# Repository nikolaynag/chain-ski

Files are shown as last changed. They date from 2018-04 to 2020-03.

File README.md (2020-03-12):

# Chain ski

This is an experimental project dedicated to a new concept of running gear. The
idea is to make something similar to continuous track, but with rollers fixed
on chain links instead of a vehicle. Each link of the track chain is a bogie
that rolls over a closed-loop rail mounted on the vehicle. Two adjacent links
share same axle. Rail contour is carefully calculated to provide continuous
whole-loop rolling. The mechanism does not involve any sliding friction and
in theory can provide a good alternative to inline  skates, at least on rough
or soft surfaces.

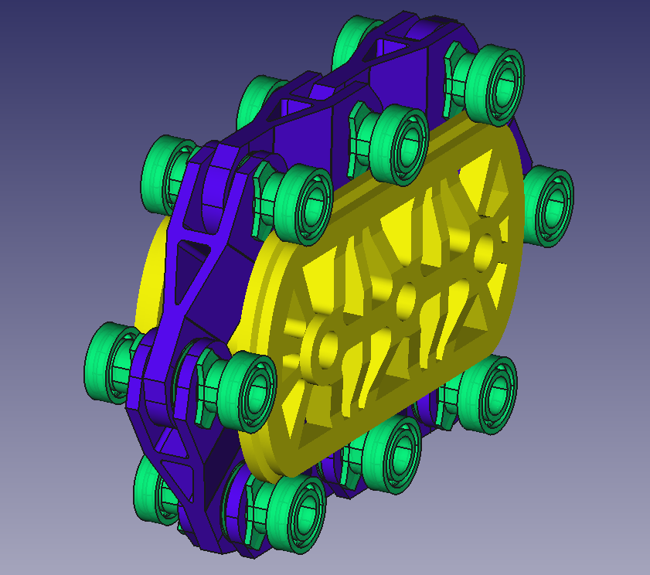
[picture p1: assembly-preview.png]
Chain ski prototype


# Construction

The mechanism is made out of 3 key elements: axle assembly, link and rail. Axle
assembly is made using standard inline skate components: ball bearings, bearing
spacers and axle. Two variants are possible: with three bearings per axis and
with two bearings per axis.

In the first case each axle assembly consists of three bearings separated by
two spacers and tightened with axle. The link is mounted between spacers on one
axle and outer race of central bearing on the other. Two bearings at sides of
each axle work as wheels rolling over the rail.

In the second case each axle assembly consists of two bearings with spacer in
between, two wheels aside and axle holding everything together. Inner races of
bearings, spacer, wheels and axle itself rotate in unison similar to railroad
car axle. Link is mounted between outer race of bearings of two axles (both
lateral and diagonal placement are possible).

In the second case link has only two points of support. It also requires
separate wheels which should be hard enough and round enough. But it is very
interesting because synchronized wheels rotation could be used for
stabilization with slightly conical wheels (like in traditional railway).

Nevertheless currently I am working on first variant between it seems simpler
to build.

# Tools and included files

3D modeling is done using FreeCAD. All models are stored in single file:
`cad-model.fcstd`. Most sizes are parameterized, initial values are set via
embedded spreadsheet. Fully assembled preview of the mechanism is available
via `FullAssemblyPreview` group (it consists of clones of all necessary parts).

## Rail contour

One of the most challenging part of design is to determine trajectory which
axes should travel when mechanism works. It could not be arbitrary because
wheels should not go off the rail all along.

After some mathematical research it was decided to make trajectory from
two lines and two specially selected ellipses. Condition for selected ellipse
is visualized in `optimal-ellipse-statement.svg` file. Numerical solution for
such ellipse is found with `wxMaxima` (see `optimal-ellipse.wxmx` file).

As far as rail contour should be equidistant from axes trajectory, we need an
equidistant of ellipse in our design. A python script `equidistant-svg.py`
creates rail contour in `svg` format using ellipse equidistant formula.
Produced `.svg` file is imported into FreeCAD model as path and used to create
rail shape (in fact, several files with different distance are used to create
rail profile).

# License and author

This project is created by [Nikolay Nagorskiy](mailto:nikolaynag@gmail.com) and
published here under the terms of [CC BY-SA 4.0](LICENSE.txt).

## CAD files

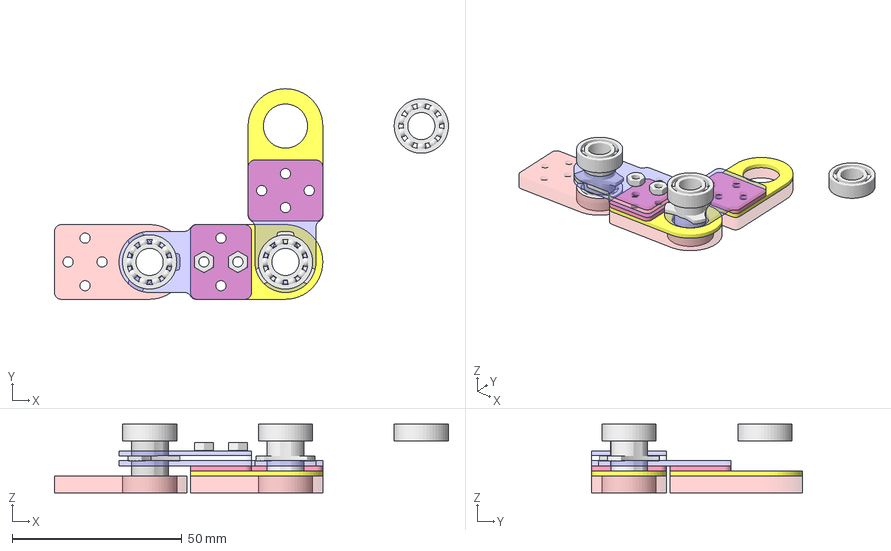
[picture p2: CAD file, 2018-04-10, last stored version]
full_parametric_model90.fcstd
116.0 x 62.0 x 20.3 mm
Base
BasePaddingRight
Spacer
BaseCapRight
SpacerHolderPaddingRight
SpacerHolderRightRight
SpacerHolderRightLeft
BearingCenter1
BearingRight1
Base2
SpecerHolderRightLeft2
Spacer2
BasePaddingRight2
BaseCapRight2
BearingRight2
BearingCenter0
Base0
BearingRight0
HoleLeftNut
HoleLeftNut001

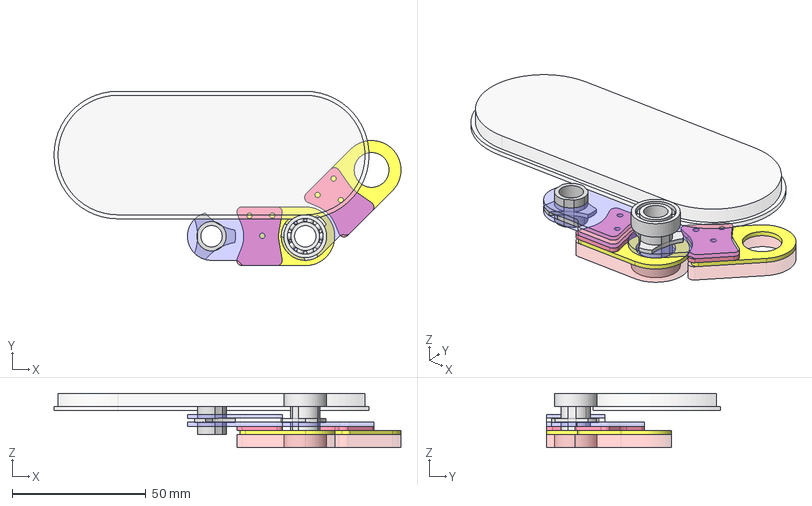
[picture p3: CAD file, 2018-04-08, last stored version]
full_parametric_model.fcstd
129.5 x 65.1 x 20.3 mm
Base
BasePaddingRight
Spacer
BaseCapRight
SpacerHolderPaddingRight
SpacerHolderRightRight
SpacerHolderRightLeft
BearingCenter1
BearingRight1
Base2
SpecerHolderRightLeft2
Spacer2
BasePaddingRight2
BaseCapRight2
RailsBase
RailsCap

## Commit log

2018-04-08 put all files into repositiory and create README
    [full_parametric_model.fcstd, full_parametric_model90.fcstd]
2018-04-09 do parts contour export, add drafts for cutting parts
    Parts countours export for cutting is described in README and
    implemented for all acril parts.
    Add concept drafts showing link assembly and whole assembly to count
    required number of parts.
    [full_parametric_model90.fcstd]
2018-04-10 make 2 variants of spacer and 3 variants of base part, create final cutting
    Make 2 variants of spacer with 0.1 mm difference in main hole radius.
    Make 3 variants of base part with 0.05 mm step in main hole radius.
    Create final cutting files.
    [full_parametric_model90.fcstd]
2020-03-09 retarget to 3d-printing, full redesign of link, add optimal ellipse rails
    For faster progress it is desided to go with 3d-printing as main
    manufacturing methos. A lot of redesign is done to minimize assembly
    after printing.
    The main link part could be printed as a whole and does not need any
    screws and nuts. There is one unsolved problem however: front bearing
    is not fixed inside a link in axial direction anymore. Will fix it soon.
    Straight test rails model is created for experiments with rail profile.
    First tests confirmed selected profile viability.
    Rails with ellipse equidistant contour are created using python script
    and svg import. Several contours with different distance together wi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
    [full_parametric_model.fcstd, full_parametric_model90.fcstd]
2020-03-12 add chain ski prototype preview image to repo and readme
